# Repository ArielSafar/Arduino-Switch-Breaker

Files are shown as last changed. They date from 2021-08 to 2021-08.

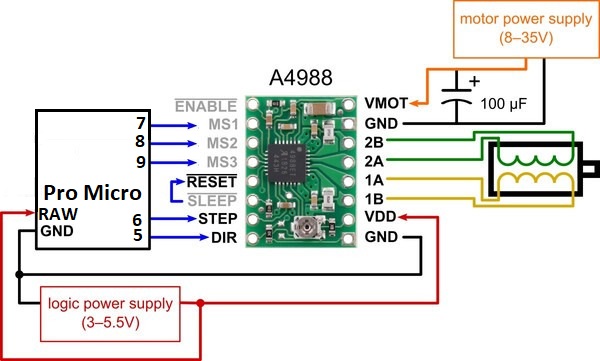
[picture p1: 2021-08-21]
circuit-diagram.jpg

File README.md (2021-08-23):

# Arduino-Switch-Breaker
this is an improved design based on flehrad's break-in machine: https://github.com/flehrad/Switch-breaker
unlike the original design this one is using a NEMA 17 stepper motor controlled by a Polulu A4988 driver
and an arduino pro micro.

The code itself is using the StepperDriver library by laurb9: https://github.com/laurb9/StepperDriver

# a little more about changes from the original design:
The center pole has been enlarged to 8mm for a 150mm lead screw.
The cams now have holes for M5 screws so they will be
held together by groups of two with a SHF8 lead screw fastener.
The motor plate has mounting holes for a bearing to hold the lead screw so it will rotate freely as possible
the center pole is bigger by 1mm than the other parts,
allowing the lead screw to float there not touching the plastic.
for mouting the beraings an extra small 90 degree part has been added

all parts were printed in petg. other materials could produce different results

https://raw.githubusercontent.com/kapyuval/Arduino-Switch-Breaker/dev/circuit-diagram.jpg

# BOM

## 3D Printed parts

 * 2 x Motor Holder
 * 4 x Cam
 * 8 x Switch Rack
 * 4 x 90 Degree Adapter

## Tools
* a soldering iron
* a file set for compensating for 3d printed parts tolerances
* (Optional) a multimeter to verify connections
* a screw driver set
* pliers for holding the nuts while you fasten them
* a pc for programming the arduino
* access to a 3d printer

## Parts

* 4x20mm M5
* 4x10mm M5
* 4x30mm M5
* 4xM5 nuts

* 1x8mm to 4mm stepper motor adapter (or get other adapter that fits your motor shaft)
* 1x150mm lead screw with 8mm diameter, 2mm pitch, 4mm lead 
* 2xSHF8 8mm lead screw fasteners
* 2xKP08 Shaft holder bearing
* 1xNEMA 17 motor (any bipolar motor will work)
* 32xDSA keycaps

* 12V dc power supply
* Polulu A4988 stepper motor driver
* arduino pro micro
* (optional) breadboard

## Pricing

* a set with a shaft, two bearing and an 8mm to 8mm adapter (if it fits your motor shaft)
recommended even of you don't use the adapter beacause shipping would be more expensive if 
you buy the bearings separately when purchased seperately
https://www.amazon.com/gp/product/B097JBT1TF/
18.69$

* a single 150mm lead screw
https://www.amazon.com/Screw-Pitch-Length-Copper-Printer/dp/B08GS7TY4J
7.99$

* 2 pcs KP08 bearing shaft holder
https://www.amazon.com/PAZIKO-Diameter-Bearing-Mounted-Support/dp/B08NK8JCJ1
8.99$

* 2 pcs SHF8 fastener
https://www.amazon.com/Aluminum-Holder-Linear-Support-Bearing/dp/B01G0ENHFE
4.29$

* M5 screw assortment.
i got this one, it's always good to have some extras
https://www.amazon.com/gp/product/B07WZHN2XS
12.99$

* Stepper motor
The specific one i used was jut one i had laying around. this model: 42SHD0217-24B
get a bipolar 4 wires motor. it's really important to invest in a good quality motor
https://www.amazon.com/DROK-2-Phrase-Universal-Electric-Engraving/dp/B06XSYP24P
17.59$

* arduino pro micro
aliexpress probably has those for cheaper
https://www.amazon.com/ATmega32U4-Replace-ATmega328-Leonardo-Interface/dp/B086JK79JJ
7.23$

* Polulu A4988 driver
https://www.amazon.com/Printer-Accessory-Reprap-Stepper-Heatsink/dp/B0868F8LDD
3.42$

* 12v power supply with a 2 wire adapter
https://www.amazon.com/dp/B01AZLA9XQ
6.99$

* dupont wire for connecting stuff
https://www.amazon.com/QQQ-Breadboard-Multicolored-Arduino-Raspberry/dp/B0925KFP3F
5.28$

* (Optional) breadboard for prototyping (or if you don't want to commit the pro micro)
you could also solder or connect directly 
https://www.amazon.com/dp/B07FYBBVYR
6.58$
breadboard/wires bundle
https://www.amazon.com/DaFuRui-Breadboard-400-Point-Multiple-Preformed/dp/B07KGQHJW8
13.99$

*(Optional - if you already have ones) DSA keycaps (x37). use a set you don't care destroying. 
those are prbably the cheapest on amazon with more than 32 keycaps
https://www.amazon.com/YMDK-Keycap-Switches-Mechanical-Keyboard/dp/B079GPVBQ2
13.5$

## Total Costs
* everything with wires only (no keycaps)
76.48$
* everything with breadboard (no keycaps)
85.19$

* DSA keycaps are another 13.99$

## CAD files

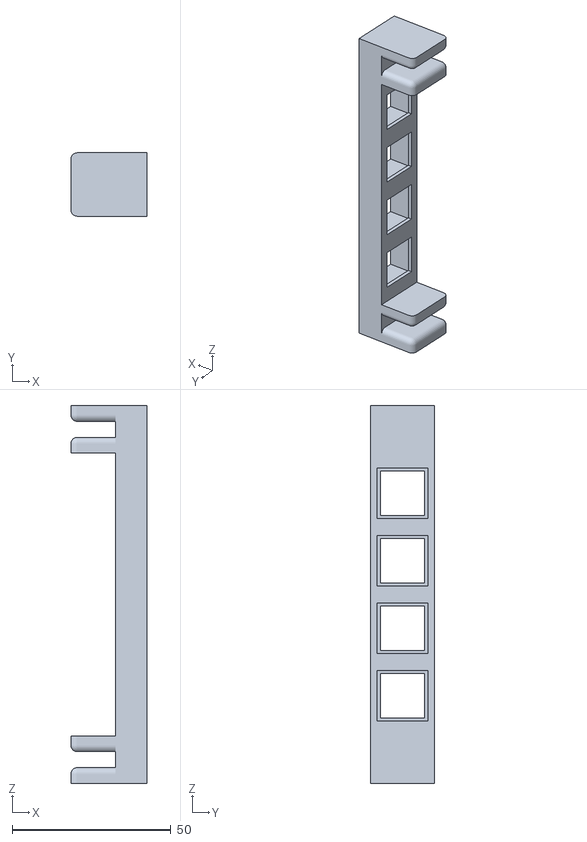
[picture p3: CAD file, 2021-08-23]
3d-models/switch-rack.stl
24.0 x 20.0 x 119.0

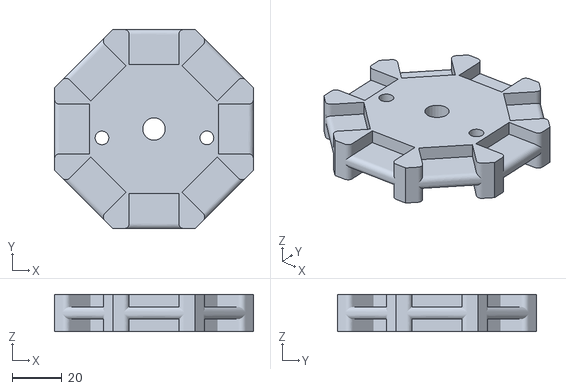
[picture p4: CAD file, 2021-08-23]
3d-models/motor-holder.stl
80.0 x 80.0 x 15.0

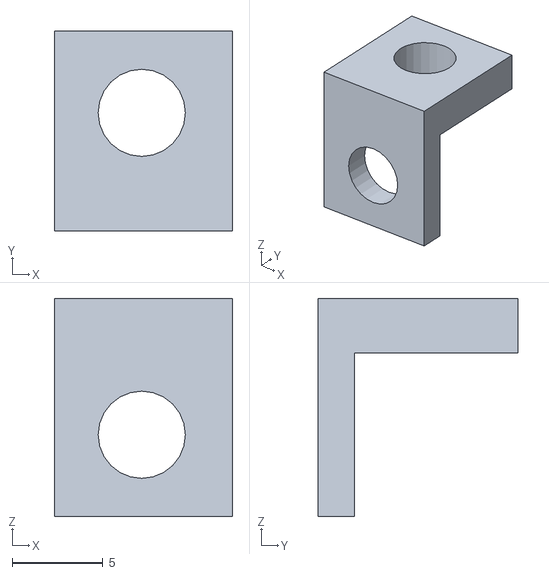
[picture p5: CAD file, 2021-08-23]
3d-models/90-degree-adapter.stl
9.81 x 11.0 x 12.0

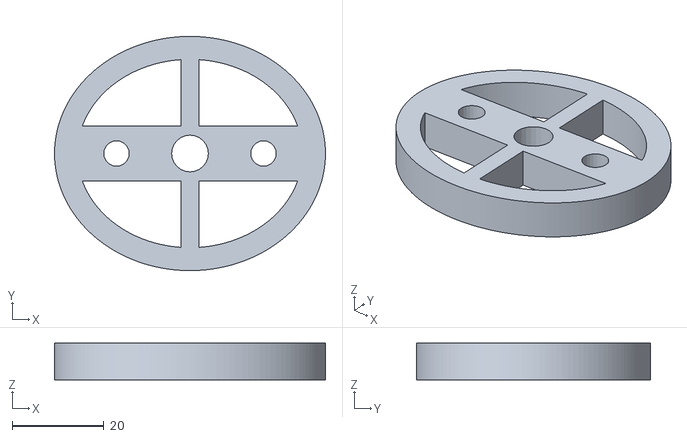
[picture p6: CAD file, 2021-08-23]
3d-models/cam.stl
59.0 x 51.0 x 8.00

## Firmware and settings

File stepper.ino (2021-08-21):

#include <Arduino.h>
#include <A4988.h>
#include <Ethernet.h>
#include <EEPROM.h>

// <!-- Stepper motor stuff -->
#define DIR 5
#define STEP 6
#define MS1 7
#define MS2 8
#define MS3 9
#define MICROSTEPS 16
#define MOTOR_STEPS 200 // using a 200-step motor (most common)

byte RPM = 120;
A4988 stepper(MOTOR_STEPS, DIR, STEP, MS1, MS2, MS3);
double cw_revolutions = 0, ccw_revolutions = 0;

enum DIRECTION
{
	CW = 1,
	CCW = -1
};

DIRECTION direction = CW;

// <!-- Network stuff -->
#define PORT 80
EthernetServer server(PORT);
EthernetClient client;
String buffer;
boolean currentLineIsBlank;

// <!-- Storage addresses -->
#define CW_REVS_ADDR 100
#define CCW_REVS_ADDR 110

void setup()
{
	byte mac_address[] = {0xDE, 0xA0, 0xB3, 0x5F, 0xFE, 0xED};
	init_serial(9600);
	init_server(server, mac_address);
	init_stepper(RPM, MICROSTEPS);

	cw_revolutions = get_revolutions_storage(CW_REVS_ADDR);
	ccw_revolutions = get_revolutions_storage(CCW_REVS_ADDR);
}

void loop()
{
	handle_motor();
	handle_network();

	// Save revolution every 100
	if (direction == CW && (int)cw_revolutions % 100 == 0 && (int)cw_revolutions == cw_revolutions)
		save_revolutions_to_storage(CW_REVS_ADDR, (int)cw_revolutions);

	if (direction == CCW && (int)ccw_revolutions % 100 == 0 && (int)ccw_revolutions == ccw_revolutions)
		save_revolutions_to_storage(CCW_REVS_ADDR, (int)ccw_revolutions);
}

// <!-- EEPROM Memory -->
unsigned int get_revolutions_storage(int addr)
{
	return (EEPROM.read(addr) << 8) + EEPROM.read(addr + 1);
}

void save_revolutions_to_storage(int addr, int revolutions)
{
	writeUnsignedIntIntoEEPROM(addr, revolutions);
}

void writeUnsignedIntIntoEEPROM(int address, unsigned int number)
{
	EEPROM.write(address, number >> 8);
	EEPROM.write(address + 1, number & 0xFF);
}

void clean_memory()
{
	cw_revolutions = 0;
	ccw_revolutions = 0;
	writeUnsignedIntIntoEEPROM(CW_REVS_ADDR, 0);
	writeUnsignedIntIntoEEPROM(CCW_REVS_ADDR, 0);
}

// <!-- Initializers -->
void init_serial(unsigned int data_rate)
{
	Serial.begin(data_rate);
	Serial.println("Serial started successfully with data rate of " + String(data_rate));
}

void init_stepper(unsigned short rpm, unsigned short microsteps)
{
	stepper.begin(rpm, microsteps);
	Serial.println("Stepper motor started successfully, set to " + String(rpm) + " RPM and step ratio to 1:" + String(microsteps));
}

void init_server(EthernetServer server, byte mac_addr[])
{
	Ethernet.begin(mac_addr);
	server.begin();
	Serial.print("Ethernet initialized successfully: ");
	Serial.println(Ethernet.localIP());
}

// <!-- Handle network stuff -->

void send_response(String json, String content_type, String status_code)
{
	client.print("HTTP/1.1 ");
	client.println(status_code);
	client.print("Content-Type: ");
	client.println(content_type);
	client.println("Access-Control-Allow-Methods: POST, GET, OPTIONS, DELETE");
	client.println("Access-Control-Allow-Origin: *");
	client.println();

	client.print(json);
}

String json(const char *key, const char *value)
{
	char buffer[30];
	sprintf(buffer, "{\"%s\":\"%s\"}", key, value);
	return String(buffer);
}

String json(const char *key, const int value)
{
	char buffer[30];
	sprintf(buffer, "{\"%s\":%d}", key, value);
	return String(buffer);
}

void handle_motor()
{
	if (RPM <= 0)
	{
		stepper.setRPM(0);
		return;
	}
	stepper.setRPM(RPM);

	if (direction == 1)
		cw_revolutions += (1 / 16.0);
	else
		ccw_revolutions += (1 / 16.0);

	stepper.rotate(360 / 16.0 * direction);
}

void handle_network()
{
	client = server.available();
	if (!client)
	{
		return;
	}

	boolean currentLineIsBlank = true;
	buffer = "";

	while (client.connected())
	{
		if (!client.available())
		{
			break;
		}

		char c = client.read(); // Read from the Ethernet shield
		buffer += c;			// Add character to string buffer
		Serial.print(c);
		// Client sent request, now waiting for response
		if (c == '\n' && !currentLineIsBlank)
		{
			Serial.println();

			if (isOptionsRequest(buffer))
			{
				client.println("HTTP/1.1 204 No Content");
				client.println("Access-Control-Allow-Methods: POST, GET, OPTIONS, DELETE");
				client.println("Access-Control-Allow-Origin: *");
				client.println();
			}
			else
			{
				send_response(handle_response(buffer), "application/json", "200 OK");
			}

			break;
		}
		if (c == '\n')
		{
			currentLineIsBlank = true;
			buffer = "";
		}
		else if (c == '\r')
		{
		}
		else
			currentLineIsBlank = false;
	}
	client.stop(); // End server
}

// This is the place to add more abilities

boolean isOptionsRequest(String buffer)
{
	return buffer.indexOf("OPTIONS") >= 0;
}

String handle_response(String buffer)
{
	if (buffer.indexOf("POST /direction=CW") >= 0)
	{
		direction = CW;
		return json("direction", "CW");
	}
	if (buffer.indexOf("POST /direction=CCW") >= 0)
	{
		direction = CCW;
		return json("direction", "CCW");
	}

	if (buffer.indexOf("POST /speed=") >= 0)
	{
		String tmp = buffer.substring(12, 15);
		RPM = tmp.toInt();
		return json("speed", RPM);
	}

	if (buffer.indexOf("DELETE /revolutions") >= 0)
	{
		clean_memory();
		return json("revolutions", 0);
	}

	if (buffer.indexOf("GET /speed") >= 0)
		return json("speed", RPM);
	if (buffer.indexOf("GET /direction") >= 0)
		return json("direction", direction == 1 ? "CW" : "CCW");
	if (buffer.indexOf("GET /revolutions?direction=CW") >= 0)
		return json("cw_revolutions", cw_revolutions);
	if (buffer.indexOf("GET /revolutions?direction=CCW") >= 0)
		return json("ccw_revolutions", ccw_revolutions);
	if (buffer.indexOf("GET /revolutions") >= 0)
		return json("revolutions", cw_revolutions + ccw_revolutions);
}

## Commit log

2021-08-20 Added circuit diagram
2021-08-21 added API to communicate with the Arduino
2021-08-21 added BOM and amazon links
2021-08-21 updated the readme with BOM and 3D printed parts checklist
2021-08-21 added the 3d models
    [90-degree-adapter.stl, cam.stl, motor-holder.stl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]
